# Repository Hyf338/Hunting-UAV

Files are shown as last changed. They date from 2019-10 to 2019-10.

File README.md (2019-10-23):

# Hunting-UAV
Hunting Unmanned Aerial Vehicle 2019 全国大学生电子设计竞赛 【B题】

<p align="center">
  
</p>

[通信协议](./Docs/README.md)

## 简介
2019集大电协 巡线无人机

本文对巡线机器人进行了初步的研究和设计，该机器人由四旋翼飞行器与检测识别模块构成。根据四旋翼飞行器飞行原理，选择合适的无刷电机作为系统动力装置，选取了功能强大且容易开发的微处理器、传感器和相关电子元器件，并做了大量的系统软硬件调试工作，最终完成了整体设计。
本机器人采用TM4C123GH6PMI单片机为主控制器，通过六轴加速度陀螺仪ICM20602采集的四旋翼欧拉角数据进行ADRC处理以保持飞机的姿态稳定；采用SPL06气压传感器以及激光测距模块GY-53L1控制巡线机器人的飞行高度；使用OpenMV实现巡检电力线路及杆塔状态。

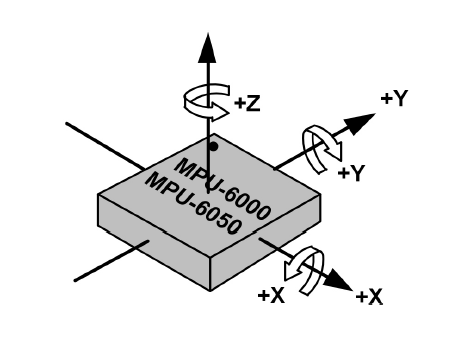
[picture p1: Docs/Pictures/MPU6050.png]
6轴坐标


#### ENU坐标系

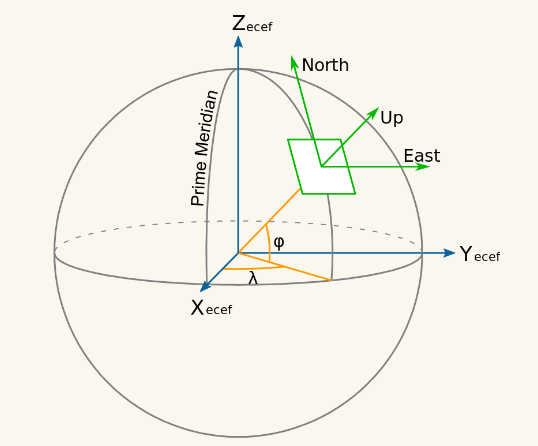
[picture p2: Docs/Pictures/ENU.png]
东南天坐标系


工具     | 描述
-------- | -----
Altium Design|PCB设计
Keil|软件编程
Solidworks|3D软件（3D打印）
123D Design|3D软件（激光切割）

| 硬件 | 描述 |
| -- | -- |
|芯片型号| TM4C123G |
|CPU| Cortex-M4 |
|主频| 80MHz |
|FLASH| 256KB |
|RAM|  32KB |
|EEPROM|  2KB |
|单元| FPU、DSP |

## 目录说明
````
+——Marine craft
|----+ Docs: 【设计文档】
|    |  tool 【调试工具】
|    |  参考文献 
|---- 3D model: 【3D模型、激光切割】
|    |  Solidworks【3D打印摄像头支架】
|    |  123D Design【激光切割】
|----+ hardware:【电路设计】  
|       Controller 【飞控主控板】
|---+ software:【软件设计】
|       ├──ETA-fly【飞控程序】
````

## 3D model
- 摄像头支架

摄像头支架

- 激光切割

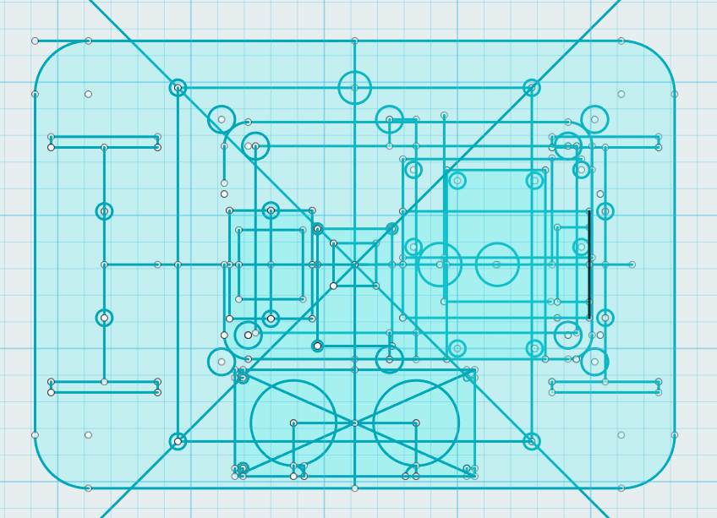
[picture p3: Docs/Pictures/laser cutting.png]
激光切割亚克力转接板


## Hardware

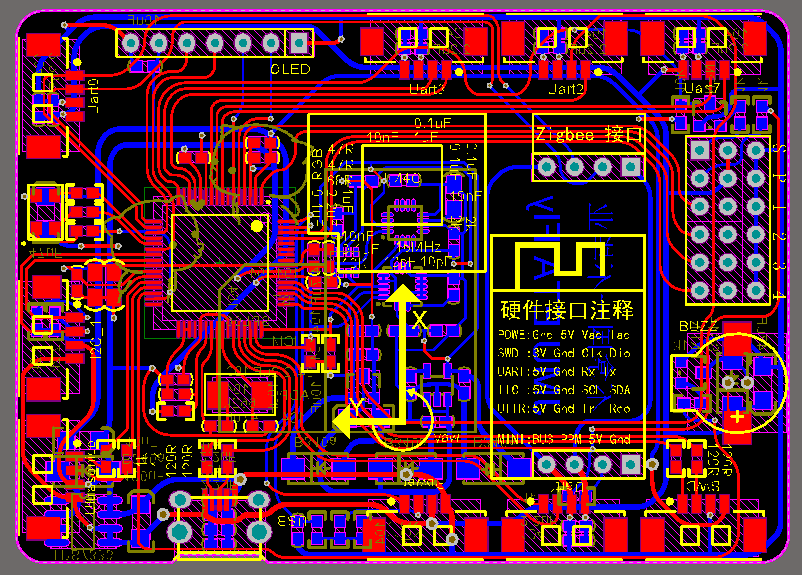
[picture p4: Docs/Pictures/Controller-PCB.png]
飞控主控


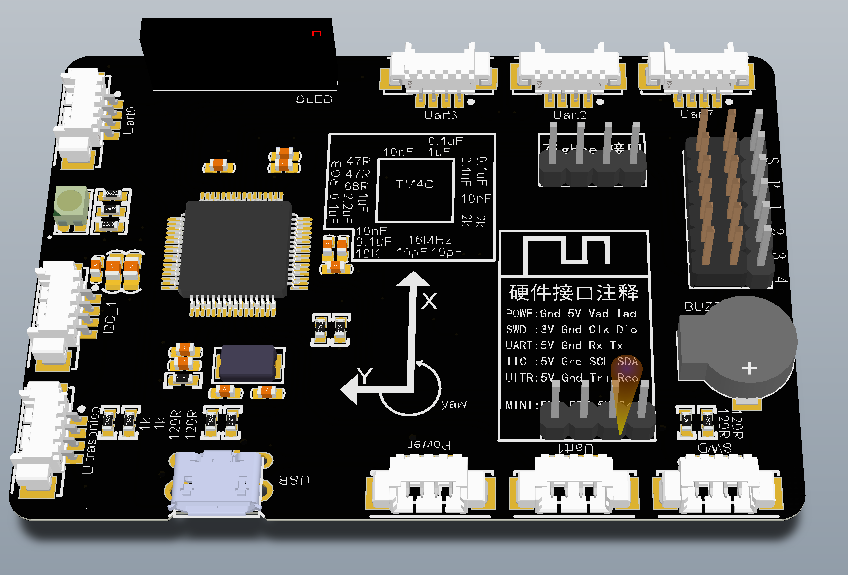
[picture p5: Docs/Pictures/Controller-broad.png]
飞控主控3D


## Sensor
- 主控与外设描述

硬件     | 描述
-------- | -----
陀螺仪  | ICM-20602
加速度计  | SPL06
磁力计  | IST8310
激光测距  |GY-53L1x
光流|优象

## 通信总协议

[通信协议](./Docs/README.md)

#### 》》协议表格中，若带 0x 开头代表该值是16进制，无0x开头，则为十进制《《
|编号 | 0| 1 | 2 | 3 | 4 | 5 | 6 | 7 | 8 | 9 | 10 |11  |12  |13  |14  |15|
| --- | --- | --- | --- | --- | --- | --- | --- | --- | --- | --- | --- | --- | --- | --- |--- |--- |
|数据包所代表 | 包头 | 包头 |模式位  | 数据长度位 |保留位  |保留位 |保留位 |保留位 | 保留位  |保留位  |保留位  | 保留位 |保留位| 保留位| 保留位|累加和校验sum|
|描述 | 0xAA| 0x55 | 1~255 | <12 |  |  |  |  |  | |  |  |  | || sum

1. AA 55为包头
2. 模式位：巡线远程模式等等
2. 数据长度位：代表后面除校验位有几位有效数据
3. 保留位：不传输
4. 校验和：从包头开始到校验位前的所有数据和的低八位

## UVA-1 && UVA-2

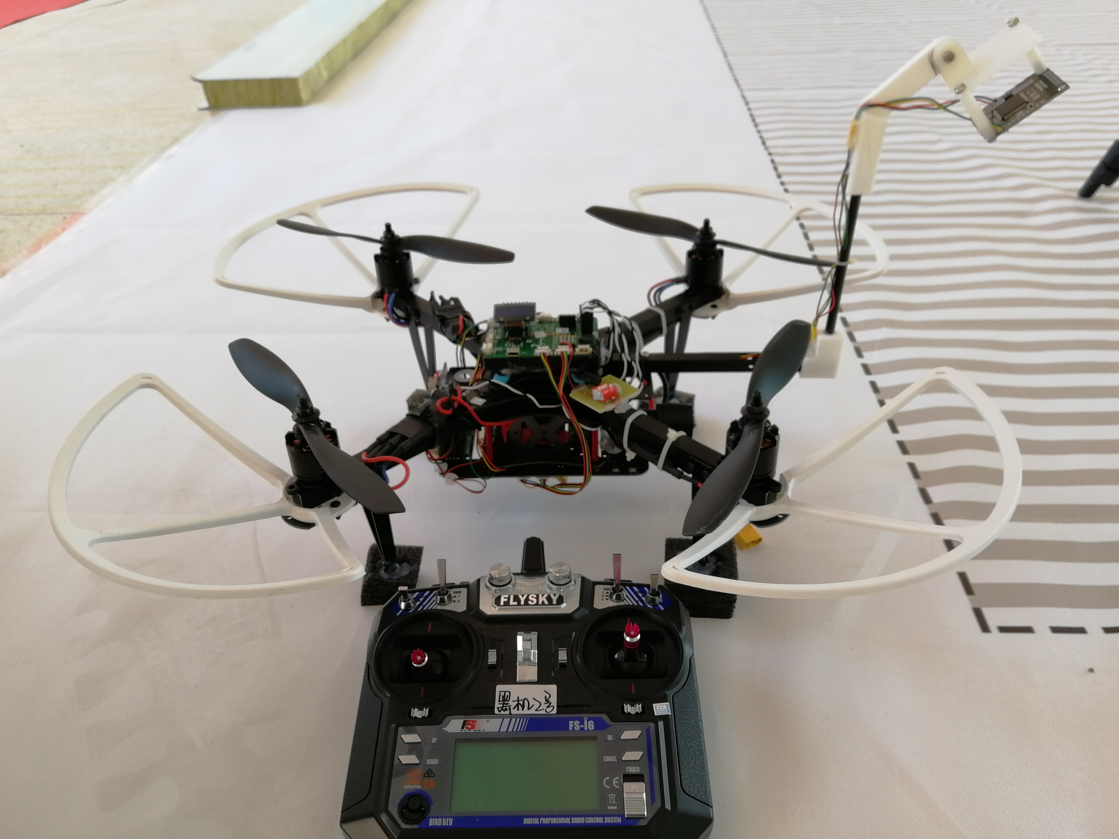
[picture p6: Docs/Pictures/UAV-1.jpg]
UVA-1


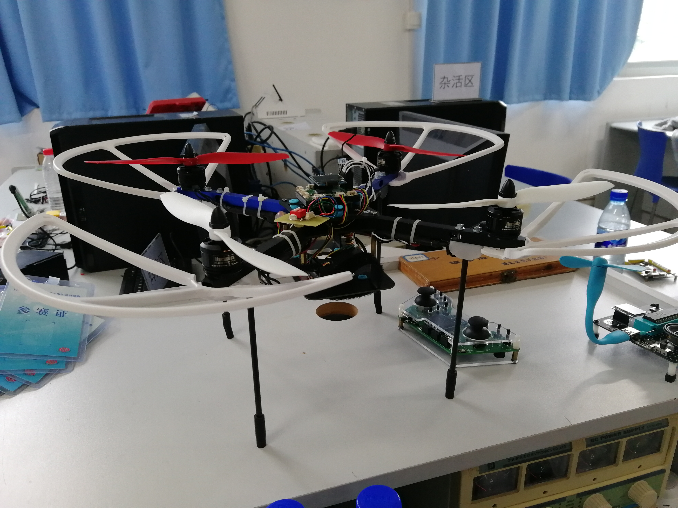
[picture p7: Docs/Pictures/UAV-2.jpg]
UVA-2


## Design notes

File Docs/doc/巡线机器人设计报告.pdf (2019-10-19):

# 2019 年全国大学生电子设计竞赛

## 巡线机器人（B 题）

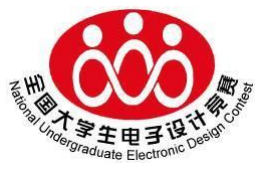
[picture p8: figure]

JD012

# 2019 年 8 月 10 日

摘要

本文对巡线机器人进行了初步的研究和设计，该机器人由四旋翼飞行器与检测识别模块

构成。根据四旋翼飞行器飞行原理，选择合适的无刷电机作为系统动力装置，选取了功能强

大且容易开发的微处理器、传感器和相关电子元器件，并做了大量的系统软硬件调试工作，

最终完成了整体设计。

本机器人采用 TM4C123GH6PMI 单片机为主控制器，通过六轴加速度陀螺仪 ICM20602 采集

的四旋翼欧拉角数据进行 ADRC 处理以保持飞机的姿态稳定；采用 SPL06 气压传感器以及激光

测距模块 GY-53L1 控制巡线机器人的飞行高度；使用 OpenMV 实现巡检电力线路及杆塔状态。

关键字：TM4C123GH6PMI 单片机、OpenMV、ICM20602 加速度陀螺仪、GY-53L1 激光测距、ADRC

控制。

目录

# 一、系统方案

本系统主要由电源模块、飞行控制模块、传感器模块组成，下面分别论证这几个模块的

选择。

## 1.1 电机的论证与选择

方案一：普通直流电机。普通直流电机有价格低廉、使用简单等优点，但其扭矩较小，

可控性差，此系统要求控制精度高、速度快、且质量要小，所以直流电机一般不能满足要求。

方案二：无刷电机是一种由电调间接控制转速的装置，具有体积小、重量轻、扭矩大的

优点。而且，电调控制无刷电机具有快速响应，控制精度高等优点。

综合以上两种方案，选择方案二。

## 1.2 空间定位传感器的论证与选择

方案一：HC-SR04 超声波模块性能稳定，测量距离精确，盲区小，用于测量四旋翼飞行

器距地面的距离。但在实际测试中发现四旋翼飞行器在飞行过程中螺旋桨的转动会对超声波

干扰较大，测量距离误差较大。

方案二：GY-53L1 数字红外测距传感器模块。工作电压 3-5v，低成本，功耗小，体积小，

安装方便。模块另外可以设置单独传感器芯片工作模式， GY-53-L1X VL53L1 作为简单传感

器模块，MCU 不参与数据处理工作。

方案三：GY-53L1 数字红外测距传感器加光流传感器，光流传感器能快速的检测水平移

动。控制简单。光流传感器对外部光照亮度有很大的依赖性，且只能在一定高度内进行检测。

考虑到测试环境在屋内，飞行高度较低等因素，我们选择方案三，采用激光加光流传感

器进行空间定位。在光线充足的情况下，可以满足题目相关要求。

## 1.3 视觉处理传感器与巡检方案

OpenMV 它是一个可编程的摄像头，通过 MicroPython 语言，可以实现逻辑应用。而且摄

像头本身内置了一些图像处理算法，我们可以很容易地在 OpenMV 所看到的内容上运行机器视

觉算法，以便在短时间内进行巡检和拍照存储。赛道分区示意图如图 1 所示：

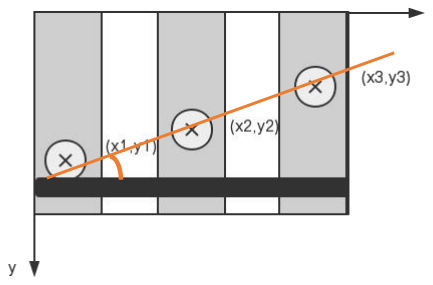
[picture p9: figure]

图 1 赛道分区示意图
分区巡线方式：通过巡线机器人实际飞行轨迹在各个区域的点与线缆的偏航角α 反馈给
飞控以达到巡线目的。 | ) 3 1

3 1

## arctan(

x x

y y -
- α = | 。

因在巡检时需要对塔杆上二维码与线缆异物上条形码进行拍照存储，因此我们又增加一

个 OpenMV 进行专门识别二维码与条形码并拍照存储。 二、系统控制理论分析

## 2.1 运动模型分析

首先以机器人起始点建立绝对坐标系，以机器人机身重心处建立无人机的相对坐标系。
我们定义我们将无人机的位置为 | T L = [x, y,z] ,定义无人机的俯仰角，翻滚角，偏转角为

T

## an =[φ,θ,ψ ] 。

我们可以将角速度转换成如下形式： | • ú

û

ù

ê
ë

é -
= | an
0

0

1 0

φ | θ φ
φ | θ φ θ
ω

### s c c

### c c s s

三维空间的欧拉角旋转矩阵为：
ú
û

ù

ê
ë

é
+ | - | -
=
φ θ | φ θ | θ
θ ψ φ | φ ψ | φ θ ψ | φ ψ | ψ θ
φ ψ | θ φ ψ | ψ φ | φ θ ψ | θ ψ
s s | | c s | | c
c c s c s | c c c s s | c s
c s s | c s c c s | s s
R

c c

通过能量守恒，我们知道电机在给定时间内消耗的能量等于螺旋桨上产生的力乘以它所排出

的空气移动的距离。
可得P·dt = F ·dx，即
dt

dx P = F 。由此可得 P T h = v

其中T 为四旋翼的推力， h v 为悬停时的速度，P 为悬停时消耗的功率，P 与角速度ω 成正比。

由此可以推出，四旋翼的总推力为：
ú
û

ù

ê
ë
é = | = ∑
∑= | 2

4

i 1

s | 0

0
k
i T | Ti | ω

设四旋翼运动时受到的阻力为 f ,假设 f 四旋翼移动速度成正比：

úû

ù

êë

é-

=

•

•

- k z
k y

k x
f | d d
d 由此可以讲运动模型概括为：L | RT f + s +

ú
û

ù

ê
ë

é-
= mg

0

0

## 2.2 控制方式论证与选择

巡线机器人结构属于 X 型分布。即螺旋桨 1 和 4 与 2 和 3 关于 X 轴对称，螺旋桨 1 和 2

与 3 和 4 关于 Y 轴对称如图 2 所示：

图 2 X 型分布

方案一：PID 算法是将偏差的比例（ Proportion）、积分（ Integral）和微分

（ Differential） 通过线性组合构成控制量，用这一控制量对被控对象进行控制。但 PID

对环境变化敏感，机器人的螺旋桨在高速旋转时，受到很强的压缩空气阻力，PID 的作用力

要很大才能维持稳定的速度，但是当低速时，空气阻力非常小，在 PID 作用力下，螺旋桨会

震动、不稳定。

方案二：ADRC 控制方式，继承了经典 PID 控制器的精华，对被控对象的数学模型几乎没

有任何要求，又在其基础上引入了基于现代控制理论的状态观测器技术，将抗干扰技术融入

到了传统 PID 控制当中去，最终设计出了适合在工程实践中广泛应用的全新控制器。传统 PID

控制都要等到误差发生后，才能去补偿控制，而 ADRC 将观察到的扰动第一时间补偿到输出端。

ADRC 在系统抗干扰，模型参数变化时的控制性能比传统的 PID 控制器有很强的优势。

综合以上两种方案，选择方案二。

# 2.3 ADRC 控制

ADRC 的核心有三大模块：微分跟踪器、扩张状态观测器和状态误差反馈控制律。基于 ADRC

的四旋翼飞行控制器,该控制器能够无稳态误差地实现悬停控制、轨迹跟踪控制。跟踪微分器

安排过渡过程，加快响应速度，同时还可以用于对数据进行滤波。扩展状态观测器设计了一

个扩展的状态量来跟踪模型未知部分和外部未知扰动的影响，然后给出控制量补偿这些扰动。

非线性误差反馈控制律给出被控对象的控制策略。ADRC 控制结构如图 3 所示：

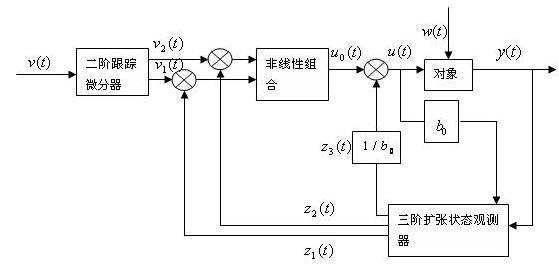
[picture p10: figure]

图 3 ADRC 控制结构

跟踪微分器的阶跃响应：

2( 1) 2( ) * ( 1( ) ( ), 2( ), , )

1( 1) 1( ) * 2( )
v k | v k h fhan v k v k v k r h
v k | v k h v k
+ = | + | -
+ = | +

扩张状态观测器：

3( 1) 3 * 3* ( 1, 2, )

2( 1) 2( ) | * ( 3( ) | 2 * ( 2, 2, ) 0 * ( ))
1( 1) 1( ) | * ( 2( ) 1* ( 1, 1, ))

1

1 2; 2 ( ) ( ); ( ) | ( 1, 2, , )
β | ε α δ
β | ε α δ
β | ε α δ ω
z k | z h | fal
z k | z k h z k | fal | b u k
z k | z k h z k | fal

y x

x x x | a t u t a t f x x | t

+ = -

+ = | + | - | +
+ = | + | -

=

= | = | + | = 非线性控制策略方程：

( ) 0( ) 3( )/ 0

0( ) | * ( 1( ), , 0) | * ( 2( ), , 0) | * ( 1, , 0)

2( ) 2( ) 2( )

1( ) 1( ) 1( )

### u k u k z k b

u k kp fal e k p | kd fal e k D | ki fal e i

### e k v k z k

e k v k z k = | -
= | + | +
= | -
= | - | α δ | α δ | α δ

# 三、控制系统硬件与软件设计

## 3.1 系统硬件电路设计 3.1.1 系统总体框图

系统总体框图如图 4 所示：

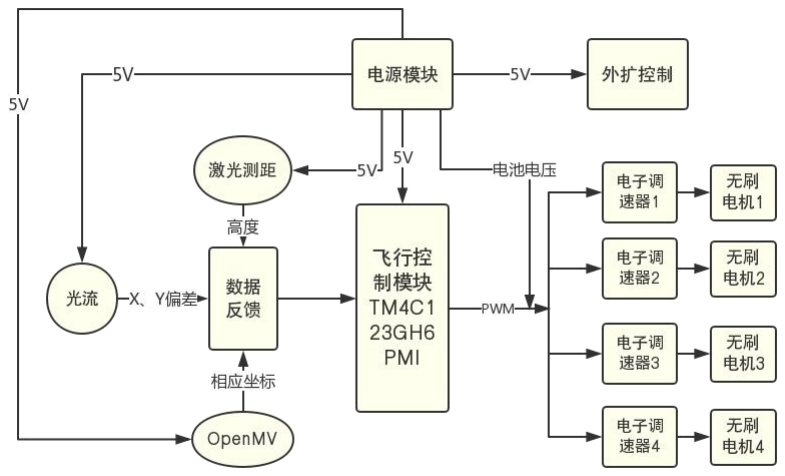
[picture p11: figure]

图 4 系统总体框图

## 3.1.2 飞行控制原理图

飞行控制模块是控制系统的核心部分。它在每个控制周期内实时处理传感器采集的数据

和飞行器的姿态信息，完成 ADRC 控制的算法，得到四旋翼飞行器的姿态和位置信息，计算出

控制量，转化为相应的控制信号驱动四个电机工作，保持四旋翼飞行器稳定飞行。原理图如

图 5 所示：

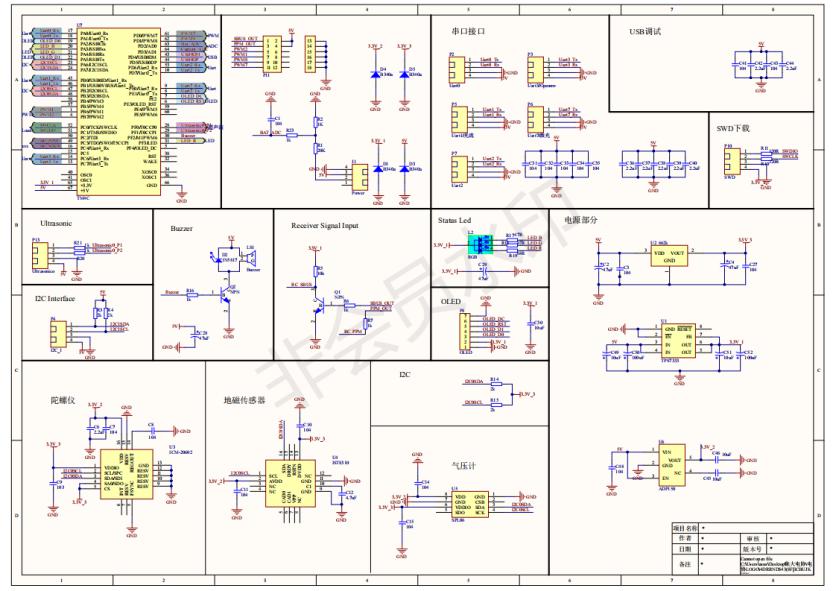
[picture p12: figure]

图 5 飞行控制

## 3.1.3 外扩控制电路

外扩控制电路是为了实现四旋翼飞行器执行相应的控制动作，激光笔实时指示所巡路线，

以及实现对飞控信息的转发。

# 3.1.4 电源管理

电源由一块 11.1~12.6V 的锂电池提供，给四个电调供电，电源通过稳压模块稳出 5V 给

飞控及外扩板供电，这样可满足各个小系统的电源要求。

## 3.2 系统软件设计 3.2.1 程序功能描述与设计思路

软件部分主要实现传感检测和 PWM 输出的更改。

（1）传感检测功能：设置高度和角度的输出信号类型。

（2）PWM 输出：根据检测的数据，通过 ADRC 算法更改 PWM 的输出。

# 3.2.2 程序流程图

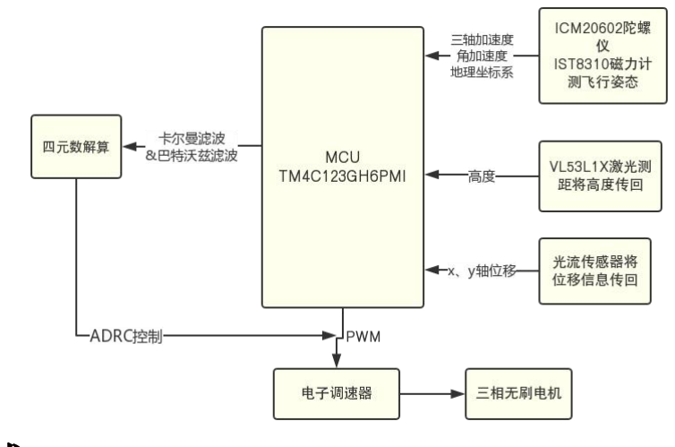
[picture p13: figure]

# 四、测试

## 4.1 测试方案与测试条件

1.测试方案：模拟考场进行测试

2.测试条件：检查多次，仿真电路和硬件电路与系统原理图完全相同，并且检查无误，

硬件电路无虚焊。

## 4.2 测试结果与分析

通过模拟考场环境对巡线机器人进行的测试的结果如下：
| 具体功能要求 | 实际测试结果
基 本 部 分 | 巡线机器人从距 A 杆塔 1 米范围内的起飞点起飞，以 1 米定高 绕杆巡检，巡检流程为：起飞→杆塔 A→电力线缆→绕杆塔 B→ 电力线缆→杆塔 A，然后稳定降落；巡检期间，巡线机器人激 光笔轨迹应落在地面虚线框内。 | 任意点起飞会存在不 稳定情况，定点起飞 情况稳定，其他基本 满足要求
| 从起飞到降落，巡线完成时间不得大于 150 秒，巡线时间越短 越好。 | 多次测试飞行时间为 50 秒左右。
| 发现线缆上异物(黄色凸起物)，巡线机器人须在与异物距离不超 过 30cm 的范围内用声或光提示。 | 发现线缆上异物灯光 闪烁提示
发 挥 部 分 | 拍摄所发现线缆异物上的条形码图片存储到 SD 卡，巡检结束 后在显示装置上清晰显示，并能用手机识别此条形码内容。 | OpenMV 实现拍摄条 形码并存储到 SD 卡
| 发现并拍摄杆塔 B 上的二维码图片存储到 SD 卡，巡检结束后在 显示装置上清晰显示，并能用手机识别此二维码内容。 | OpenMV 拍摄塔杆 B 上的二维码并存储到 SD 卡
| 拍摄每张条形码、二维码图片存储的照片数不得超过 3 张。 | 可满足要求
| 停机状况下，在巡线机器人某一旋翼轴下方悬挂一质量为 100g 的 高度平稳悬停 10 秒以上，且摆动范围不得大于±25cm。 配重，然后巡线机器人在图 3 所示环形圆板上自主起飞，并在 1 米 | 可满足要求

结果分析：经测试，系统基本可以满足基本要求和发挥部分，根据上述测试结果可以得

出以下结论：
1、经过多次测试发现实际与理论差距太大，巡线机器人飞行不稳定时会影响 OpenMV

与机器人通信出现错误，导致机器人飞行姿态会处于不稳定状态。
2、通过微调 ADRC 参数使机器人起飞平衡。

3、通过调节加速度计可使机器人按要求飞行，减小误差。

综上所述，基本可以达到预期目标，说明我们的硬件和软件的设计基本趋于合理，达到

# 要求。 五、参考文献

[1]韩京清. 从 PID 技术到"自抗扰控制"技术[J]. 控制工程, 2002, 9(3):13-18. [2]夏长亮, 李正军, 杨荣,等. 基于自抗扰控制器的无刷直流电机控制系统[J]. 中国电机工程

学报, 2005, 25(2):82-86. [3]陈小龙, 唐强, 车军,等. 基于人工视觉的四旋翼飞行器室内定位与控制[J]. 兵工自动化, 2012(5):61-64. [4]曹凯, 马贝, 王翔武. 四旋翼飞行器控制系统设计[J]. 计算机系统应用, 2018, 27(1):61-65. [5]佚名. 四旋翼飞行器基于视觉的运动目标检测与跟踪[J]. 2014.

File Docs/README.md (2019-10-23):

# 【通信总协议】
### 【最终协议以此为准】
#### 》》协议表格中，若带 0x 开头代表该值是16进制，无0x开头，则为十进制《《
|编号 | 0| 1 | 2 | 3 | 4 | 5 | 6 | 7 | 8 | 9 | 10 |11  |12  |13  |14  |15|
| --- | --- | --- | --- | --- | --- | --- | --- | --- | --- | --- | --- | --- | --- | --- |--- |--- |
|数据包所代表 | 包头 | 包头 |模式位  | 数据长度位 |保留位  |保留位 |保留位 |保留位 | 保留位  |保留位  |保留位  | 保留位 |保留位| 保留位| 保留位|累加和校验sum|
|描述 | 0xAA| 0x55 | 1~255 | <12 |  |  |  |  |  | |  |  |  | || sum

1. AA 55为包头
2. 模式位：巡线远程模式等等
2. 数据长度位：代表后面除校验位有几位有效数据
3. 保留位：不传输
4. 校验和：从包头开始到校验位前的所有数据和的低八位

* * *
#### 一：远程调参——1-3
|编号 | 0| 1 | 2 | 3 | 4 | 5 | 6 | 7 |
| --- | --- | --- | --- | --- | --- | --- | --- | --- |
|数据包所代表 | 包头 | 包头 |模式位  | 数据长度位 |参数序号  |参数高8位 |参数低8位 |累加和校验sum|
|描述 | 0xAA| 0x55 | 1~3 | 0x03 |1~10 |xx|xx| sum

**例如：AA 55 01 03 01 81 25 AA**

1. 模式位：
    * 01：巡线模式相关参数修改
    * 02：寻色块模式相关参数修改
    * 03：穿框模式相关参数修改
2. 数据长度位：0x03代表3位有效数据
3. 参数序号：0x01代表修改第1参数数据
    * 01：巡线模式相关参数序号——参数序号1~10
    * 02：寻色块模式相关参数序号——参数序号1~10
    * 03：穿框模式相关参数序号——参数序号1~10
2. 参数高8位：0x81
3. 参数低8位：0x25，结合高8位为0x8125

* * *

#### 二：查询变量模式——9
##### 1、地面端：
|编号 | 0| 1 | 2 | 3 | 4 | 5 |
| --- | --- | --- | --- | --- | --- | --- |
|数据包所代表 | 包头 | 包头 |模式位  | 数据长度位 |查询序号  |累加和校验sum|
|描述 | 0xAA| 0x55 | 9 | 1 |1~3 | sum

1. 模式位：9查询参数模式
2. 查询序号：
    * 01：查询巡线模式相关参数——参数序号1~10
    * 02：查询寻色块模式相关参数——参数序号1~10
    * 03：查询穿框模式相关参数——参数序号1~10

##### 9、飞控端返回：
|编号 | 0| 1 | 2 | 3 | 4 | 5 | 6 | 7 |
| --- | --- | --- | --- | --- | --- | --- | --- | --- |
|数据包所代表 | 包头 | 包头 |查询模式位说明  | 数据长度位 |参数序号  |参数高8位 |参数低8位 |累加和校验sum|
|描述 | 0xAA| 0x55 | 1~3 | 0x03 |1~10 |xx|xx| sum

1. 查询模式位说明
    * 01：返回巡线模式相关参数——参数序号1~10
    * 02：返回寻色块模式相关参数——参数序号1~10
    * 03：返回穿框模式相关参数——参数序号1~10

* * *
#### 三：openmv通信
##### 1、寻找单色块：
|编号 |0| 1| 2 | 3 | 4 | 5 | 
| --- | --- | --- | --- | --- | --- | --- |
|数据包所代表 | 包头 | 包头 |模式位  | 数据长度位 |识别为  | 累加和校验|
|描述 | AA| 55 | 11 | 0x01  | 0或1 | sum

##### 2、寻找线：
|编号 | 1| 2 | 3 | 4 | 5 | 6 | 7 | 8 | 9 | 10 | 11|
| --- | --- | --- | --- | --- | --- | --- | --- | --- | --- | --- | --- |
|数据包所代表 | 包头 | 包头 |模式位  | 数据长度位 |1区X  |1区Y  |2区X |2区Y | 3区X  |3区Y|累加和校验|
|描述 | AA| 55 | 12 | 0x06 | ||||| | sum

* X：0-160
* Y：0~120

##### 3、条形码:
|编号 | 1| 2 | 3 | 4 | 5 | 6 | 
| --- | --- | --- | --- | --- | --- | --- |
|数据包所代表 | 包头 | 包头 |模式位  | 数据长度位 |标志位|累加和校验|
|描述 | AA| 55 | 13 | 0x01 |  0或者1 |  sum| 

##### 4、二维码:
|编号 | 1| 2 | 3 | 4 | 5 | 6 | 
| --- | --- | --- | --- | --- | --- | --- |
|数据包所代表 | 包头 | 包头 |模式位  | 数据长度位 |标志位|累加和校验|
|描述 | AA| 55 | 14 | 0x01 |  0或者1 |  sum| 

##### 5、拍摄返回:
|编号 | 1| 2 | 3 | 4 | 5 | 6 |  
| --- | --- | --- | --- | --- | --- | --- |
|数据包所代表 | 包头 | 包头 |模式位  | 数据长度位 |标志位 |累加和校验|
|描述 | AA| 55 | 15 | 0x01 |0或者1 |  sum| 

##### 6、拍摄开始:
|编号 | 1| 2 | 3 | 4 | 5 | 6 |  
| --- | --- | --- | --- | --- | --- | --- |
|数据包所代表 | 包头 | 包头 |模式位  | 数据长度位 |标志位 |累加和校验|
|描述 | AA| 55 | 16 | 0x01 |0或者1 |  sum| 

##### 7、转弯标志:
|编号 | 1| 2 | 3 | 4 | 5 | 6 |  
| --- | --- | --- | --- | --- | --- | --- |
|数据包所代表 | 包头 | 包头 |模式位  | 数据长度位 |标志位 |累加和校验|
|描述 | AA| 55 | 17 | 0x01 |0或者1 |  sum| 

##### 9、飞控指令：
|编号 | 0| 1 | 2 | 3 | 4 | 5 |
| --- | --- | --- | --- | --- | --- | --- |
|数据包所代表 | 包头 | 包头 |模式位  | 数据长度位 |控制指令  |累加和校验sum|
|描述 | 0xAA| 0x55 | 19 | 1 |>1 | sum

- 控制指令：
    - 01：分区巡线模式
    - 02：色块模式
    - 03：巡线模式
    - 04：找圆
    - 05：找十字
    - 其它非0：不识别

- 切换模式后需要大概2-3秒的缓冲时间（重新初始化openmv）

* * *
#### 四：树莓派通信
##### 1、穿框：
|编号 | 1| 2 | 3 | 4 | 5 | 6 | 7 | 8 | 9 | 10 | 11 |
| --- | --- | --- | --- | --- | --- | --- | --- | --- | --- | --- | --- |
|数据包所代表 | 包头 | 包头 |模式位  | 数据长度位 |距离框的简单距离 | 框中心坐标x高8位  | 框中心坐标x低8位  |框中心坐标y高8位  | 框中心坐标y低8位 | 识别标志位| 累加和校验|
|描述 | 0xAA| 0x55 | 21 | 0x06 |  |  |  |  |  |0或1 | sum

- 距离框的简单距离：单位cm，最大255cm
- 框距离：（x,y），画幅左上角（0，0）
- 识别标志：0x01为识别到 0x00未识别到

##### 2、识别数字和字母：
|编号 | 1| 2 | 3 | 4 | 5 | 6 | 7 |
| --- | --- | --- | --- | --- | --- | --- | --- |
|数据包所代表 | 包头 | 包头 |模式位  | 数据长度位 |数字和字母 | 识别标志位| 累加和校验|
|描述 |0xAA|0x55 | 22 | 0x02 |  |0或1 | sum

- 数字和字母：0~9代表数字0~9；11~36代表26个英文字母
- 识别标志：0x01为识别到 0x00未识别到

##### 9、飞控指令：
|编号 | 0| 1 | 2 | 3 | 4 | 5 |
| --- | --- | --- | --- | --- | --- | --- |
|数据包所代表 | 包头 | 包头 |模式位  | 数据长度位 |控制指令  |累加和校验sum|
|描述 | 0xAA| 0x55 | 29 | 1 |0~3 | sum

- 控制指令：
    - 00：不进行识别操作
    - 01：穿框模式
    - 02：识别数字模式
    - 03：识别字母模式

* * *
#### 五：多功能执行端
##### 1、激光等外设：(由飞控发送)
|编号 | 0| 1 | 2 | 3 | 4 | 5 |
| --- | --- | --- | --- | --- | --- | --- |
|数据包所代表 | 包头 | 包头 |模式位  | 数据长度位 |控制指令  |累加和校验sum|
|描述 | 0xAA| 0x55 | 31 | 1 |0 ~ 8 | sum

0：关激光——关蜂鸣器——关灯
* 控制指令——1：关闭激光
* 控制指令——2：开启激光
* 控制指令——3：关蜂鸣器
* 控制指令——4：开蜂鸣器
* 控制指令——5：关灯
* 控制指令——6：开灯
* 控制指令——7：舵机张开
* 控制指令——8：舵机闭合
##### 2、电压检测：（发送给地面端）
|编号 | 0| 1 | 2 | 3 | 4 | 5 |6|
| --- | --- | --- | --- | --- | --- | --- | --- |
|数据包所代表 | 包头 | 包头 |模式位  | 数据长度位 |高八位  |低八位|累加和校验sum|
|描述 | 0xAA| 0x55 | 32 | 2 |xx| xx|sum

* 检测到电压值*100发送给地面站

##### 3、高度返回：
|编号 | 0| 1 | 2 | 3 | 4 | 5 |6|
| --- | --- | --- | --- | --- | --- | --- | --- |
|数据包所代表 | 包头 | 包头 |模式位  | 数据长度位 |高八位  |低八位|累加和校验sum|
|描述 | 0xAA| 0x55 | 33 | 2 |xx| xx|sum

##### 4、模式输入：
|编号 | 0| 1 | 2 | 3 |  4 |5|
| --- | --- | --- | --- | --- | --- | --- |
|数据包所代表 | 包头 | 包头 |模式位  | 数据长度位 | 数据位  |累加和校验sum|
|描述 | 0xAA| 0x55 | 34 | 1 |xx |sum

* 数据位：1~16为拨码开关的16种模式，0xDB（即219）为一键起飞模式

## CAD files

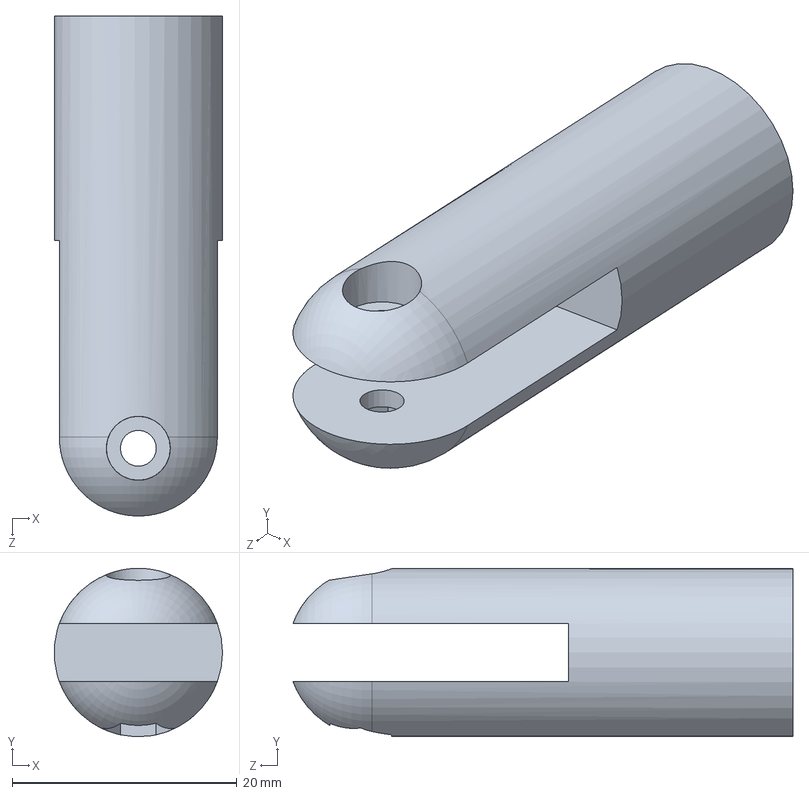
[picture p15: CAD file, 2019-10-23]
3D model/Solidworks/转换头连杆.SLDPRT
15.0 x 15.0 x 44.5 mm

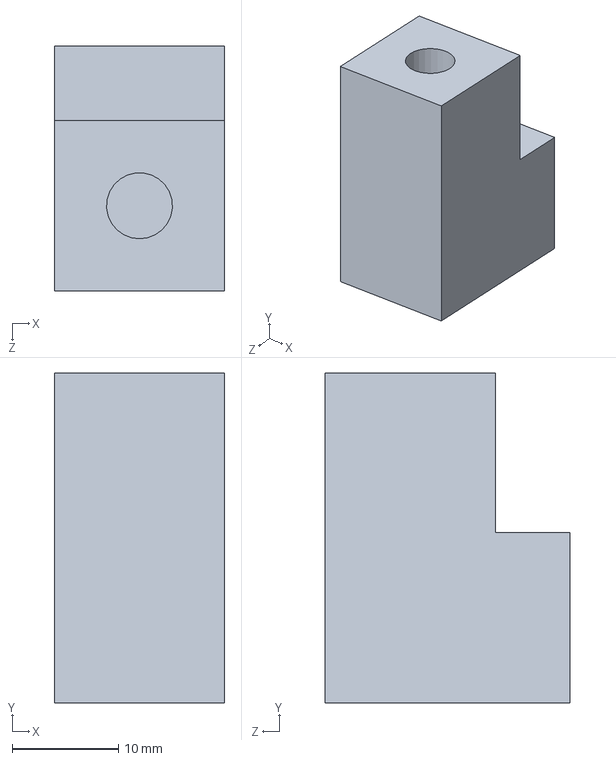
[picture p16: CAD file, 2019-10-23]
3D model/Solidworks/转换头.SLDPRT
16.0 x 31.0 x 23.0 mm

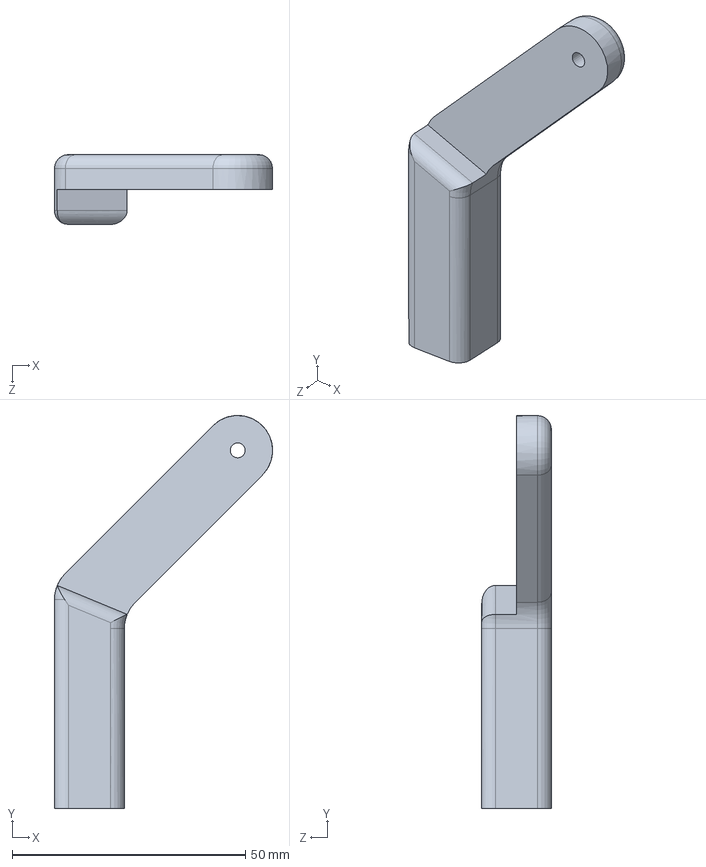
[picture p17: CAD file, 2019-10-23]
3D model/Solidworks/新连杆135度.SLDPRT
46.8 x 84.3 x 15.0 mm

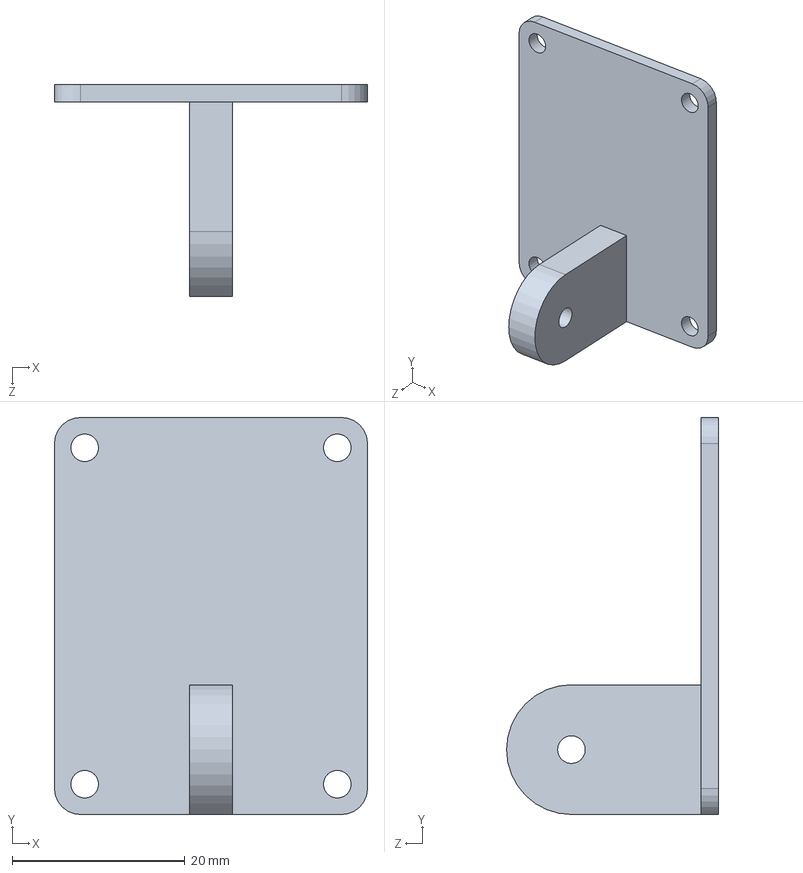
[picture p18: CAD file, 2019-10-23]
3D model/Solidworks/零件6.SLDPRT
36.2 x 45.9 x 24.5 mm

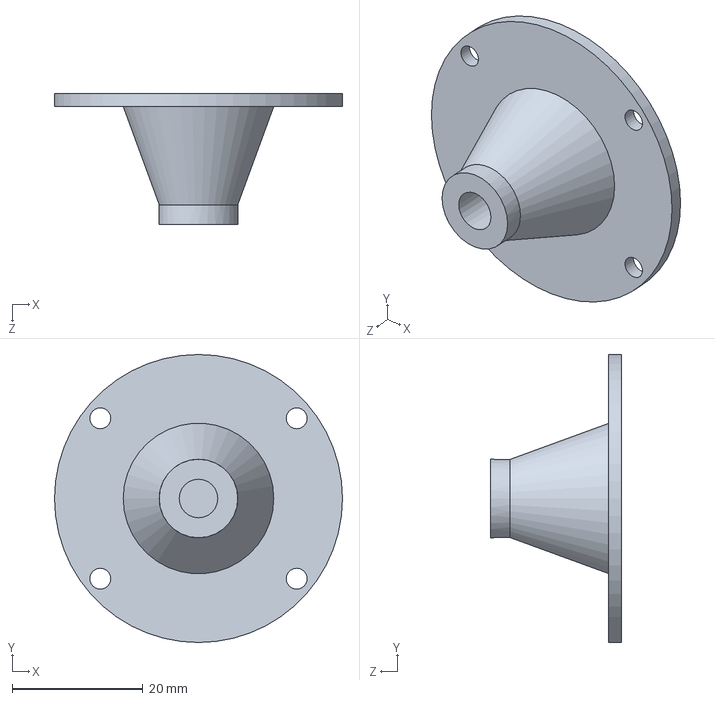
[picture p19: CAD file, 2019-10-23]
3D model/Solidworks/底座.SLDPRT
44.0 x 44.0 x 20.0 mm

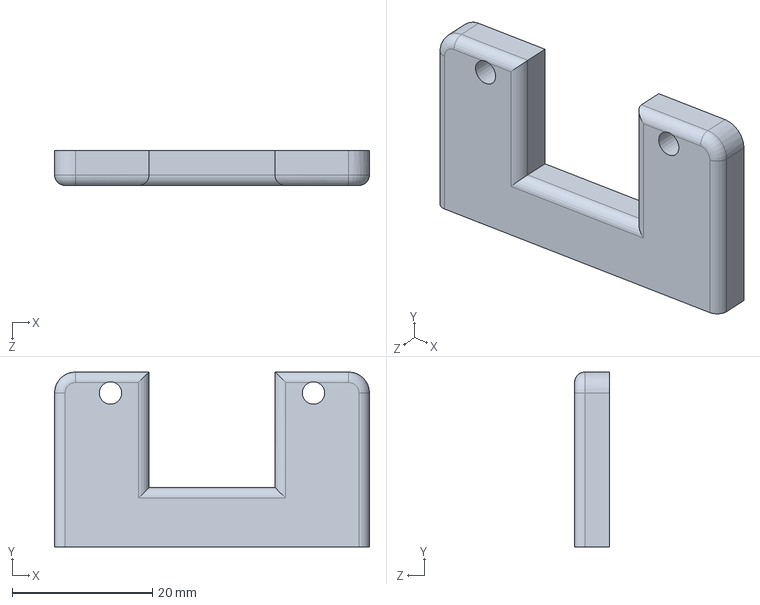
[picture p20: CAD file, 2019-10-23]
3D model/Solidworks/长焦openmv.SLDPRT
45.0 x 25.0 x 5.00 mm

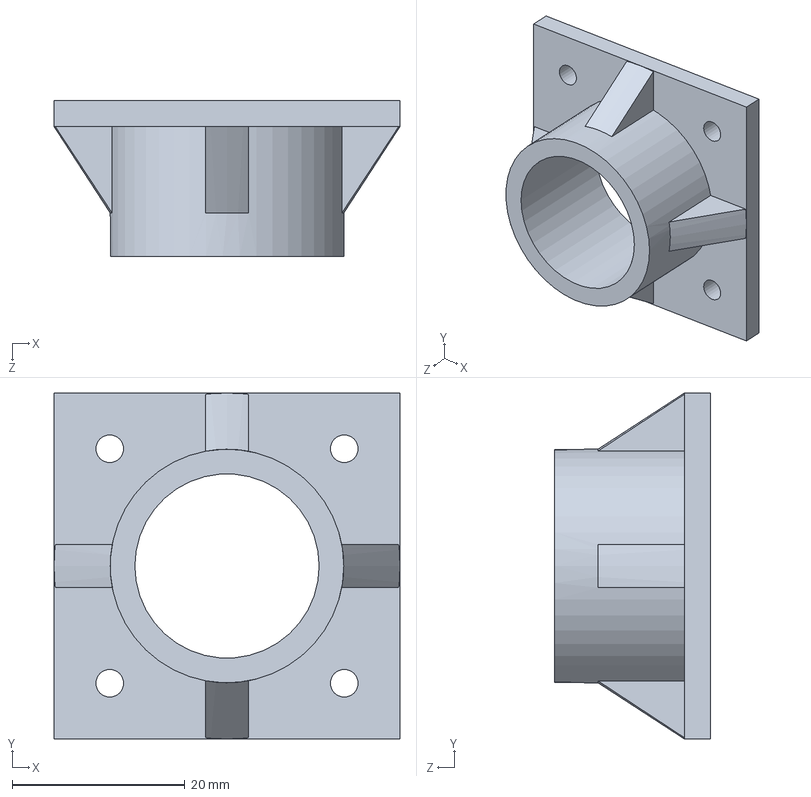
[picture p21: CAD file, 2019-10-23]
3D model/Solidworks/00011.SLDPRT
40.0 x 40.0 x 18.0 mm

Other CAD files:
3D model/Solidworks/新连杆.dwg
3D model/Solidworks/连杆.STL
3D model/Solidworks/延长转换.STL
3D model/Solidworks/openMV板.STL
3D model/Solidworks/底座.STL
3D model/Solidworks/新连杆135度.STL
3D model/Solidworks/转换头（连杆）.SLDPRT
3D model/Solidworks/长焦openmv.STL
3D model/Solidworks/长焦openmv.dwg

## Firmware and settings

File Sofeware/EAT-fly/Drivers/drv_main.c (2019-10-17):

#include "Basic.h"
#include "drv_main.h"

#include "drv_uDMA.h"
#include "drv_LED.h"
#include "drv_Sensors.h"
#include "drv_USB.h"
#include "drv_OLED.h"
#include "drv_Receiver.h"
#include "drv_PWMOut.h"
#include "drv_Ultrasonic.h"
#include "drv_OpticalFlow.h"
#include "drv_GPS.h"
#include "drv_Uart2.h"
#include "drv_SDI.h"
#include "drv_adc.h"





#include "drv_GY53.h"
#include "drv_Uart0.h"

void init_Drivers()
{
	init_drv_uDMA();
	init_drv_LED();
	init_drv_OLED();
	init_drv_PWMOut();
	
//	PWM_PullUpAll();
//	delay( 4.0f );
//	PWM_PullDownAll();
	
	init_drv_Sensors();
	init_drv_USB();	
	init_drv_Receiver();	
	init_drv_Ultrasonic();
	init_drv_OpticalFlow();
//	init_drv_GPS();
	init_drv_Uart2();
	init_drv_SDI();
	init_drv_ADC();
	
	init_drv_Uart0();
	init_drv_GY53();
}

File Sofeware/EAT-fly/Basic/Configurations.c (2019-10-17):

#include "Basic.h"
#include "Configurations.h"
#include <string.h>

#include "eeprom.h"
#include "flash.h"
#include "sysctl.h"

#include "Sensors.h"

#define CfgLength 512
static uint32_t configurations[ CfgLength ];

//本页设置见excel表：ACFly EDU EEPROM分配
//每种设置分为三个函数：
//Cfg_set_initial_xxx ：用于初始化设置
//Cfg_get_xxx ：用于读取设置
//Cfg_update_xxx ：用于更新设置并写入eeprom

/*加速度计校准*/
	//10开始为加速度校准数据
	#define Accelerometer_Calib_Start 10
	#define Accelerometer_Calib_Group_Length 10
	#define Accelerometer_Calib_Offset_StartIndex 0
	#define Accelerometer_Calib_Sensivitity_StartIndex 3
	
	void Cfg_set_initial_AccelerometerOffset( uint8_t sensor , vector3_float offset )
	{
		if( sensor >= IMU_Sensors_Count )
			return;
		memcpy( &configurations[ Accelerometer_Calib_Start + sensor*Accelerometer_Calib_Group_Length + Accelerometer_Calib_Offset_StartIndex ] ,\
			&offset , 3*sizeof(float) );
	}
	vector3_float Cfg_get_AccelerometerOffset( uint8_t sensor )
	{
		vector3_float offset = { 0, 0, 0 };
		if( sensor >= IMU_Sensors_Count )
			return offset;
		memcpy( &offset , \
			&configurations[ Accelerometer_Calib_Start + sensor*Accelerometer_Calib_Group_Length + Accelerometer_Calib_Offset_StartIndex ] ,\
			3*sizeof(float) );
		return offset;
	}
	bool Cfg_update_AccelerometerOffset( uint8_t sensor , vector3_float offset )
	{
		if( sensor >= IMU_Sensors_Count )
			return false;
		uint16_t cfg_num = Accelerometer_Calib_Start + sensor*Accelerometer_Calib_Group_Length + Accelerometer_Calib_Offset_StartIndex;
		memcpy( &configurations[ cfg_num ] , &offset , 3*sizeof(float) );
		return !EEPROMProgram( &configurations[cfg_num] , cfg_num*4 , 3*sizeof(float) );
	}
	
	void Cfg_set_initial_AccelerometerSensivitity( uint8_t sensor , vector3_float Sensivitity )
	{
		if( sensor >= IMU_Sensors_Count )
			return;
		memcpy( &configurations[ Accelerometer_Calib_Start + sensor*Accelerometer_Calib_Group_Length + Accelerometer_Calib_Sensivitity_StartIndex ] ,\
			&Sensivitity , 3*sizeof(float) );
	}
	vector3_float Cfg_get_AccelerometerSensivitity( uint8_t sensor )
	{
		vector3_float Sensivitity = { 0, 0, 0 };
		if( sensor >= IMU_Sensors_Count )
			return Sensivitity;
		memcpy( &Sensivitity , \
			&configurations[ Accelerometer_Calib_Start + sensor*Accelerometer_Calib_Group_Length + Accelerometer_Calib_Sensivitity_StartIndex ] ,\
			3*sizeof(float) );
		return Sensivitity;
	}
	bool Cfg_update_AccelerometerSensivitity( uint8_t sensor , vector3_float Sensivitity )
	{
		if( sensor >= IMU_Sensors_Count )
			return false;
		uint16_t cfg_num = Accelerometer_Calib_Start + sensor*Accelerometer_Calib_Group_Length + Accelerometer_Calib_Sensivitity_StartIndex;
		memcpy( &configurations[ cfg_num ] , &Sensivitity , 3*sizeof(float) );
		return !EEPROMProgram( &configurations[cfg_num] , cfg_num*4 , 3*sizeof(float) );
	}
/*加速度计校准*/
	
/*陀螺校准*/
	//40开始为陀螺校准数据
	#define Gyroscope_Calib_Start 40
	#define Gyroscope_Calib_Group_Length 10
	#define Gyroscope_Calib_Offset_StartIndex 0
	#define Gyroscope_Calib_Sensivitity_StartIndex 3
	
	void Cfg_set_initial_GyroscopeOffset( uint8_t sensor , vector3_float offset )
	{
		if( sensor >= IMU_Sensors_Count )
			return;
		memcpy( &configurations[ Gyroscope_Calib_Start + sensor*Gyroscope_Calib_Group_Length + Gyroscope_Calib_Offset_StartIndex ] ,\
			&offset , 3*sizeof(float) );
	}
	vector3_float Cfg_get_GyroscopeOffset( uint8_t sensor )
	{
		vector3_float offset = { 0, 0, 0 };
		if( sensor >= IMU_Sensors_Count )
			return offset;
		memcpy( &offset , \
			&configurations[ Gyroscope_Calib_Start + sensor*Gyroscope_Calib_Group_Length + Gyroscope_Calib_Offset_StartIndex ] ,\
			3*sizeof(float) );
		return offset;
	}
	bool Cfg_update_GyroscopeOffset( uint8_t sensor , vector3_float offset )
	{
		if( sensor >= IMU_Sensors_Count )
			return false;
		uint16_t cfg_num = Gyroscope_Calib_Start + sensor*Gyroscope_Calib_Group_Length + Gyroscope_Calib_Offset_StartIndex;
		memcpy( &configurations[ cfg_num ] , &offset , 3*sizeof(float) );
		return !EEPROMProgram( &configurations[cfg_num] , cfg_num*4 , 3*sizeof(float) );
	}
	
	void Cfg_set_initial_GyroscopeSensivitity( uint8_t sensor , vector3_float Sensivitity )
	{
		if( sensor >= IMU_Sensors_Count )
			return;
		memcpy( &configurations[ Gyroscope_Calib_Start + sensor*Gyroscope_Calib_Group_Length + Gyroscope_Calib_Sensivitity_StartIndex ] ,\
			&Sensivitity , 3*sizeof(float) );
	}
	vector3_float Cfg_get_GyroscopeSensivitity( uint8_t sensor )
	{
		vector3_float Sensivitity = { 0, 0, 0 };
		if( sensor >= IMU_Sensors_Count )
			return Sensivitity;
		memcpy( &Sensivitity , \
			&configurations[ Gyroscope_Calib_Start + sensor*Gyroscope_Calib_Group_Length + Gyroscope_Calib_Sensivitity_StartIndex ] ,\
			3*sizeof(float) );
		return Sensivitity;
	}
	bool Cfg_update_GyroscopeSensivitity( uint8_t sensor , vector3_float Sensivitity )
	{
		if( sensor >= IMU_Sensors_Count )
			return false;
		uint16_t cfg_num = Gyroscope_Calib_Start + sensor*Gyroscope_Calib_Group_Length + Gyroscope_Calib_Sensivitity_StartIndex;
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

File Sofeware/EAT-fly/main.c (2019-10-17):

#include "TM4C123GH6PM.h"

#include <stdio.h>
#include <rt_heap.h>
#include <stdlib.h>

#include "Basic.h"
#include "drv_main.h"
#include "MS_main.h"
#include "STS.h"
#include "Modes.h"
#include "DebugComm.h"
#include "ctrl_Main.h"
#include "Configurations.h"
#include "CommuLink.h"
#include "drv_PWMOut.h"
#include "drv_EEPROM.h"

#if 1 //如果没有这段，则需要在target选项中选择使用USE microLIB

	__asm(".global __use_no_semihosting\n\t") ;//注释本行, 方法1
		FILE __stdout;

		void _sys_exit(int x)
		{
			x = x;
		}

		//__use_no_semihosting was requested, but _ttywrch was referenced, 增加如下函数, 方法2
		void _ttywrch(int ch)
		{
			ch = ch;
		}
		
		char *_sys_command_string(char *cmd, int len)
		{
				return 0;
		}
#endif

int main()
{
	init_Basic();
	init_drv_EEPROM();
	init_MS();
	init_ControlSystem();
	init_Drivers();
	
	init_Configurations();
	
	init_Modes();
	init_CommuLink();
	
	init_Debug();
	//while(1);
	STS_Run();
}

void HardFault_Handler()
{
	//错误中断拉低所有输出
	PWM_PullDownAll();
}

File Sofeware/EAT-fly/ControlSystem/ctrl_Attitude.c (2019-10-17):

//朱文杰 20190101
//带模型ESO+反步姿态控制器
//悬停油门无参数观测器
//风力扰动观测器
//多旋翼优先级动力分配
//电机推力非线性修正
//论文正在发表
//！！请勿用于商业用途！！
//！！抄袭必究！！



#include "Basic.h"
#include "ctrl_Attitude.h"

#include "ControlSystem.h"
#include "MeasurementSystem.h"
#include "Configurations.h"
#include "drv_PWMOut.h"
#include "Receiver.h"
#include "Sensors.h"

#include "AC_Math.h"
#include "Quaternion.h"
#include "TD4.h"
#include "Filters_Butter.h"
#include "ESO_AngularRate.h"
#include "ESO_h.h"

/*状态观测器*/
	//高度ESO
	static ESO_h ESO_height;
	static float hover_throttle = 0;
	static float WindDisturbance_x = 0;
	static float WindDisturbance_y = 0;
	static bool inFlight = false;
	static inline void update_output_throttle( float throttle , float h )
	{
		vector3_float AccENU = get_AccelerationCtrl();
		float output_minimum_throttle = Cfg_get_MotorStartingThrottle();
		float lean_cosin = get_lean_angle_cosin();
		
		//观测悬停油门
		float r_throttle = throttle - output_minimum_throttle;
		if( r_throttle < 0 )
			r_throttle = 0;
		r_throttle *= lean_cosin;
		ESO_h_update_u( &ESO_height , r_throttle );
		hover_throttle = ESO_h_run( &ESO_height , AccENU.z , h ) + output_minimum_throttle;
		
		//更新飞行状态
		static uint16_t onGround_counter = 0;
		if( inFlight == false )
		{
			onGround_counter = 0;
			if( AccENU.z > 20 && throttle > output_minimum_throttle + 5 )
				inFlight = true;
		}
		else
		{
			if( hover_throttle < output_minimum_throttle + 2 && \
					in_symmetry_range_float( vector3_float_square( AccENU ) , 20*20 ) && \
					in_symmetry_range_float( vector3_float_square( get_VelocityENU() ) , 25*25 ) \
				)
			{
				if( ++onGround_counter >= 300 )
					inFlight = false;
			}
			else
				onGround_counter = 0;
		}
		
		//观测水平分力
		if( inFlight )
		{
			vector3_float active_force_xy_vec = Quaternion_rotate_axis_z( get_history_Airframe_attitude( 0.42f / 10 ) );
			if( lean_cosin < 0.3f )
				lean_cosin = 0.3f;
			active_force_xy_vec = vector3_float_mult( active_force_xy_vec , ( AccENU.z + constG ) / lean_cosin );
			vector3_float WindDisturbance_xy;
			WindDisturbance_xy.x = AccENU.x - active_force_xy_vec.x;
			WindDisturbance_xy.y = AccENU.y - active_force_xy_vec.y;
			
			float lp_factor = 2 * PI_f * (1.0f/200) * 0.3f;
			WindDisturbance_x += lp_factor * ( WindDisturbance_xy.x - WindDisturbance_x );
			WindDisturbance_y += lp_factor * ( WindDisturbance_xy.y - WindDisturbance_y );
		}
		else
			WindDisturbance_x = WindDisturbance_y = 0;
	}
/*状态观测器*/
	
/*观测器*/
	float get_hover_throttle()
	{
		return hover_throttle;
	}
	bool get_is_inFlight()
	{
		return inFlight;
	}
	float get_WindDisturbance_x()
	{
		return WindDisturbance_x;
	}
	float get_WindDisturbance_y()
	{
		return WindDisturbance_y;
	}
/*观测器*/

/*模式及期望*/
	//期望TD4滤波器
	static TD4 Target_tracker[3];
	//姿态ESO
	static ESO_AngularRate ESO[3];
	//扰动滤波器
	static Filter_Butter2_LP_float disturbance_filter[3];

	//姿态控制模式
	static bool Attitude_Control_Enabled = false;
	static Attitude_ControlMode RollPitch_ControlMode = Attitude_ControlMode_Angle;
	static Attitude_ControlMode Yaw_ControlMode = Attitude_ControlMode_Angle;

	static float throttle = 0;
	static float target_Roll;
	static float target_Pitch;
	static float target_Yaw;
	static vector3_float target_AngularRate;
	
	float get_Target_Throttle()
	{
		return throttle;
	}
	
	bool Attitude_Control_Enable()
	{
		if( Attitude_Control_Enabled == true ||\
			get_Attitude_Measurement_System_Status() != Measurement_System_Status_Ready )
			return false;
		
		Attitude_Control_Enabled = true;
		target_Yaw = Quaternion_getYaw( get_Airframe_attitude() );
		RollPitch_ControlMode = Attitude_ControlMode_Angle;
		Yaw_ControlMode = Attitude_ControlMode_Angle;
		
		/*初始化*/
			//初始化期望TD4滤波器
			TD4_init( &Target_tracker[0] , Cfg_get_RPYCtrl_TD4Pn( 0 , 1 ) , Cfg_get_RPYCtrl_TD4Pn( 0 , 2 ) , Cfg_get_RPYCtrl_TD4Pn( 0 , 3 ) , Cfg_get_RPYCtrl_TD4Pn( 0 , 4 ) );
			TD4_init( &Target_tracker[1] , Cfg_get_RPYCtrl_TD4Pn( 1 , 1 ) , Cfg_get_RPYCtrl_TD4Pn( 1 , 2 ) , Cfg_get_RPYCtrl_TD4Pn( 1 , 3 ) , Cfg_get_RPYCtrl_TD4Pn( 1 , 4 ) );
			TD4_init( &Target_tracker[2] , Cfg_get_RPYCtrl_TD4Pn( 2 , 1 ) , Cfg_get_RPYCtrl_TD4Pn( 2 , 2 ) , Cfg_get_RPYCtrl_TD4Pn( 2 , 3 ) , Cfg_get_RPYCtrl_TD4Pn( 2 , 4 ) );
			
			//初始化姿态ESO
			init_ESO_AngularRate( &ESO[0] , Cfg_get_MotorT(0) , Cfg_get_RPYCtrl_b(0) , 0.7f , 10 );
			init_ESO_AngularRate( &ESO[1] , Cfg_get_MotorT(1) , Cfg_get_RPYCtrl_b(1) , 0.7f , 10 );
			init_ESO_AngularRate( &ESO[2] , 1.0f/200 , Cfg_get_RPYCtrl_b(2) , 0.7f , 10 );
		/*初始化*/
		
		return true;
	}
	bool Attitude_Control_Disable()
	{
		if( Attitude_Control_Enabled == false )
			return false;		
		Attitude_Control_Enabled = false;
		Altitude_Control_Disable();
		Position_Control_Disable();
		return true;
	}
	
	bool Attitude_Control_set_Throttle( float thr )
	{
		if( Attitude_Control_Enabled == false )
			return false;
		throttle = thr;
		return true;
	}
	float Attitude_Control_get_Target_Roll() { return target_Roll; }
	float Attitude_Control_get_Target_Pitch() { return target_Pitch; }
	float Attitude_Control_get_Target_Yaw() { return target_Yaw; }
	bool Attitude_Control_set_Target_RollPitch( float Roll , float Pitch )
	{
		float angle = safe_sqrt_f( Roll*Roll + Pitch*Pitch );
		if( angle > 0.8f )
		{
			float scale = 0.8f / angle;
			Roll *= scale;
			Pitch *= scale;
		}
		
		if( Attitude_Control_Enabled == false )
			return false;
		target_Roll = Roll;
		target_Pitch = Pitch;
		RollPitch_ControlMode = Attitude_ControlMode_Angle;
		return true;
	}
	bool Attitude_Control_set_Target_Yaw( float Yaw )
	{
		if( Attitude_Control_Enabled == false )
			return false;
		target_Yaw = Yaw;
		if( Yaw_ControlMode != Attitude_ControlMode_Angle )
		{
			Target_tracker[2].x1 = Quaternion_getYaw( get_Airframe_attitude() );
			Yaw_ControlMode = Attitude_ControlMode_Angle;
		}
		return true;
	}
	bool Attitude_Control_set_Target_YawRelative( float Yaw )
	{
		if( Attitude_Control_Enabled == false )
			return false;
		float currentYaw = Quaternion_getYaw( get_Airframe_attitude() );
		if( Yaw_ControlMode != Attitude_ControlMode_Angle )
		{
			Target_tracker[2].x1 = currentYaw;
			Yaw_ControlMode = Attitude_ControlMode_Angle;
		}
		target_Yaw = Target_tracker[2].x1 + Yaw;
		return true;
	}
	bool Attitude_Control_set_Target_YawRate( float YawRate )
	{
		if( Attitude_Control_Enabled == false )
			return false;
		target_AngularRate.z = YawRate;
		Yaw_ControlMode = Attitude_ControlMode_AngularRate;
		return true;
	}
	bool Attitude_Control_set_YawLock()
	{
		if( Attitude_Control_Enabled == false )
			return false;
		if( Yaw_ControlMode == Attitude_ControlMode_AngularRate )
			Yaw_ControlMode = Attitude_ControlMode_Locking;
		return true;
	}
/*模式及期望*/
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

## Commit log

2019-10-17 【更新】提交文档
    [Configurations.h, UAV_Controller.PrjPcb]
2019-10-18 【更新】提交飞控一体板
    [UAV_Controller.PrjPcb]
2019-10-18 【更新】提交飞控代码
    [Configurations.h]
2019-10-19 【更新】完善说明文档
    [Configurations.h, UAV_Controller.PrjPcb, 飞控一体板.PrjPcb]
2019-10-23 【更新】提交Solidworks文件
    [00011.SLDPRT, openMV板.STL, 底座.SLDPRT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]
2019-10-23 【更新】提交通信协议
2019-10-23 【更新】完善文档
2020-01-03 【提交】提交参考文档
